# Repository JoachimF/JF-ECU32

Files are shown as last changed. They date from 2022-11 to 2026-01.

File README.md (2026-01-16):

# JF-ECU32
RC Jet Engine ECU
Details ici : https://www.usinages.com/threads/creation-dun-ecu-opensource-pour-micro-reacteur.160245/

## Démarrage du projet d'ECU opensource pour réacteurs

### Fonctionnalitées :

- Démarrage GAZ/KERO
- Fonctionnement du réacteur
- Surveillance des paramètres
- Redémarrage en vol

### Composants :
- Processeur ESP32
- Interface sonde K MAX31855

### Entrées :
- Entrée 2S - 3S pour accus LIPO ou LIION
- Entrée PPM - Gaz ou SBUS
- Entrée PPM - AUX
- Entrée compte tours IR ou HALL
- Entrée sonde K (module MAX6675 ou MAX31865)
- Entrée pression (à voir le capteur selon les plages de pression 2 bars max?)

### Sorties :
- Sortie PPM pour le moteur de démarrage
- Sortie PWM/PPM pour la pompe 10A ou ESC brushless
- Sortie PWM/PPM pour ESC de pompe numéro 2 (fumigène ou redondance, comme sur les grandeurs)
- Sorties pour 2 électrovannes (KERO/GAZ - KERO/KERO) 1A
- Sortie pour une bougies Glow ou Kero 10A
- Sortie FPORT FRSky (télémétrie)
- Sortie LED W2812

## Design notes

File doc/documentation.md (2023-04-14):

#Documentation

Detail du fonctionnement :

Les taches :

- Main
- Serveur HTTP
- Log
- ECU
- Inputs
- Htop (pour le debug)

Détail des taches :

- Main
Lance les autres taches

- Serveur HTTP
Gère l'interface WEB, s'arrete au bout de 60 secondes si pas de connection
Coupe le Wifi aussi

- Log
Enregistre dans un fichier téléchargeable par le Web tous les parmètres a partir de démarrage du moteur jusqu'a l'extinction

- ECU
Tache prioritaire qui gère le moteur en pilotant les sorties en fonction des entrée

- Inputs
Tache prioritaire qui lit les entrées

- Htop
Gestionnaire de tache qui donne le pourcentage d'utilisation du processeur par tache

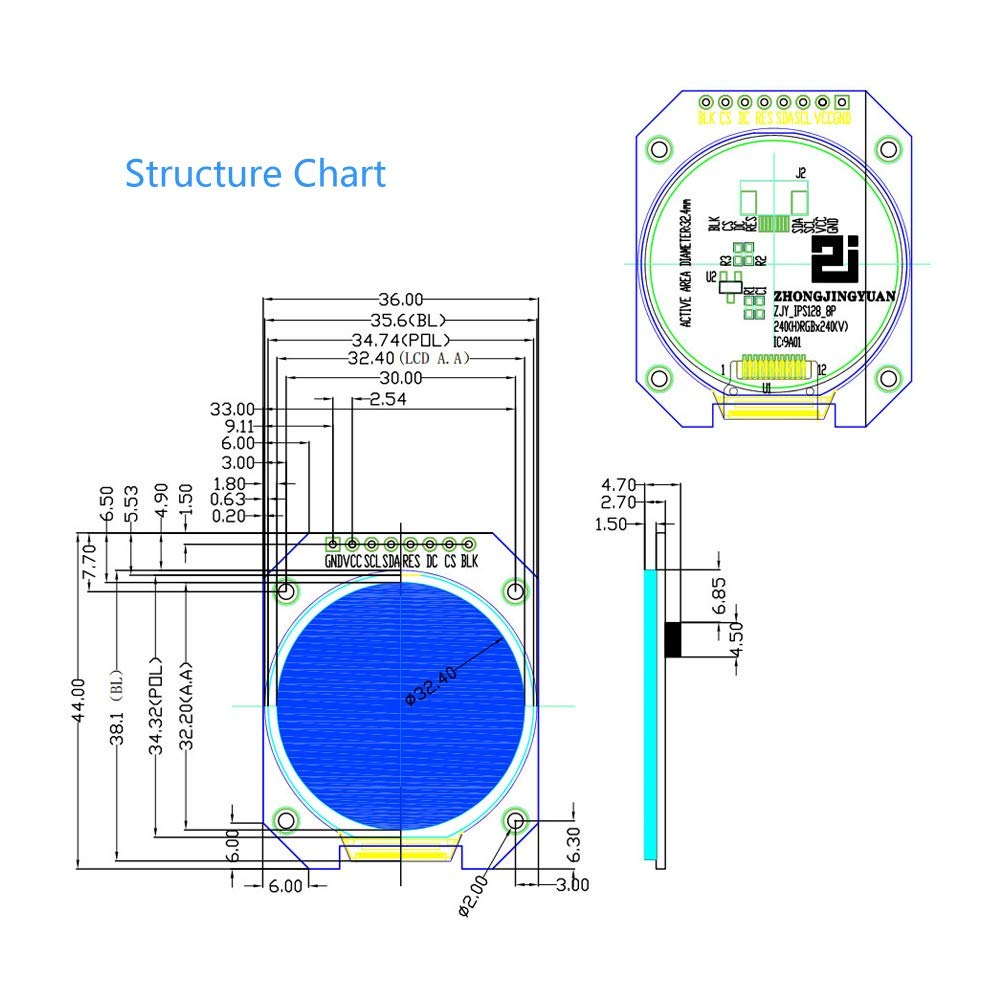
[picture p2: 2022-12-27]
Hardware/61U9lrLj2jL._SL1000_.jpg

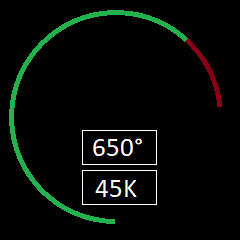
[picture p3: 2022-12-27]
doc/lcd.png

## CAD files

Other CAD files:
lcd.SLDPRT

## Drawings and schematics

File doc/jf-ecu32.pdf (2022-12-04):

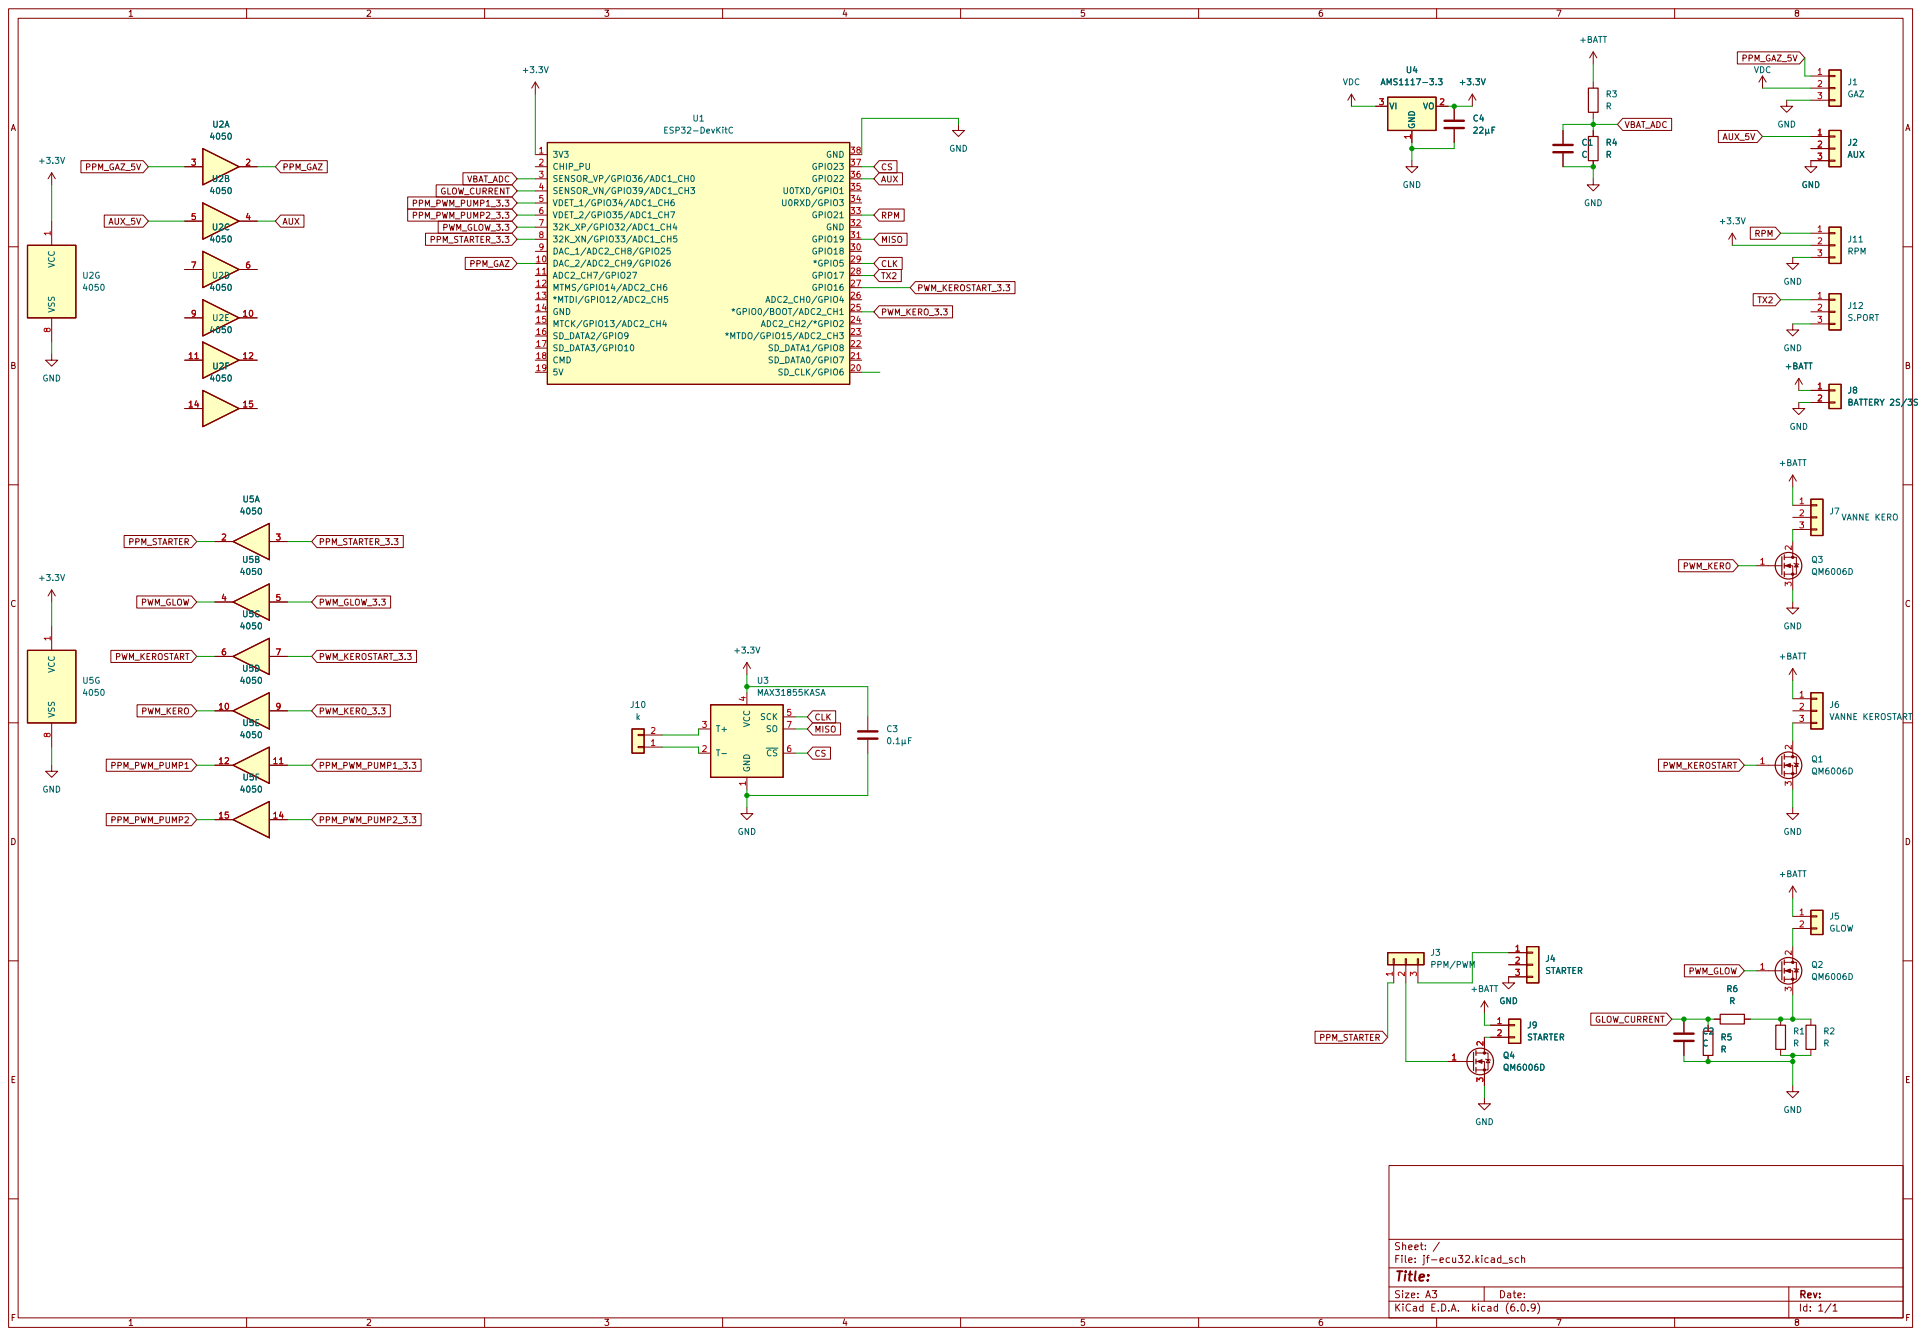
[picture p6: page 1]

+BATT GND GND GND

4 SCK 5 ~{CS} 6 SO 7 U3MAX31855KASA GND

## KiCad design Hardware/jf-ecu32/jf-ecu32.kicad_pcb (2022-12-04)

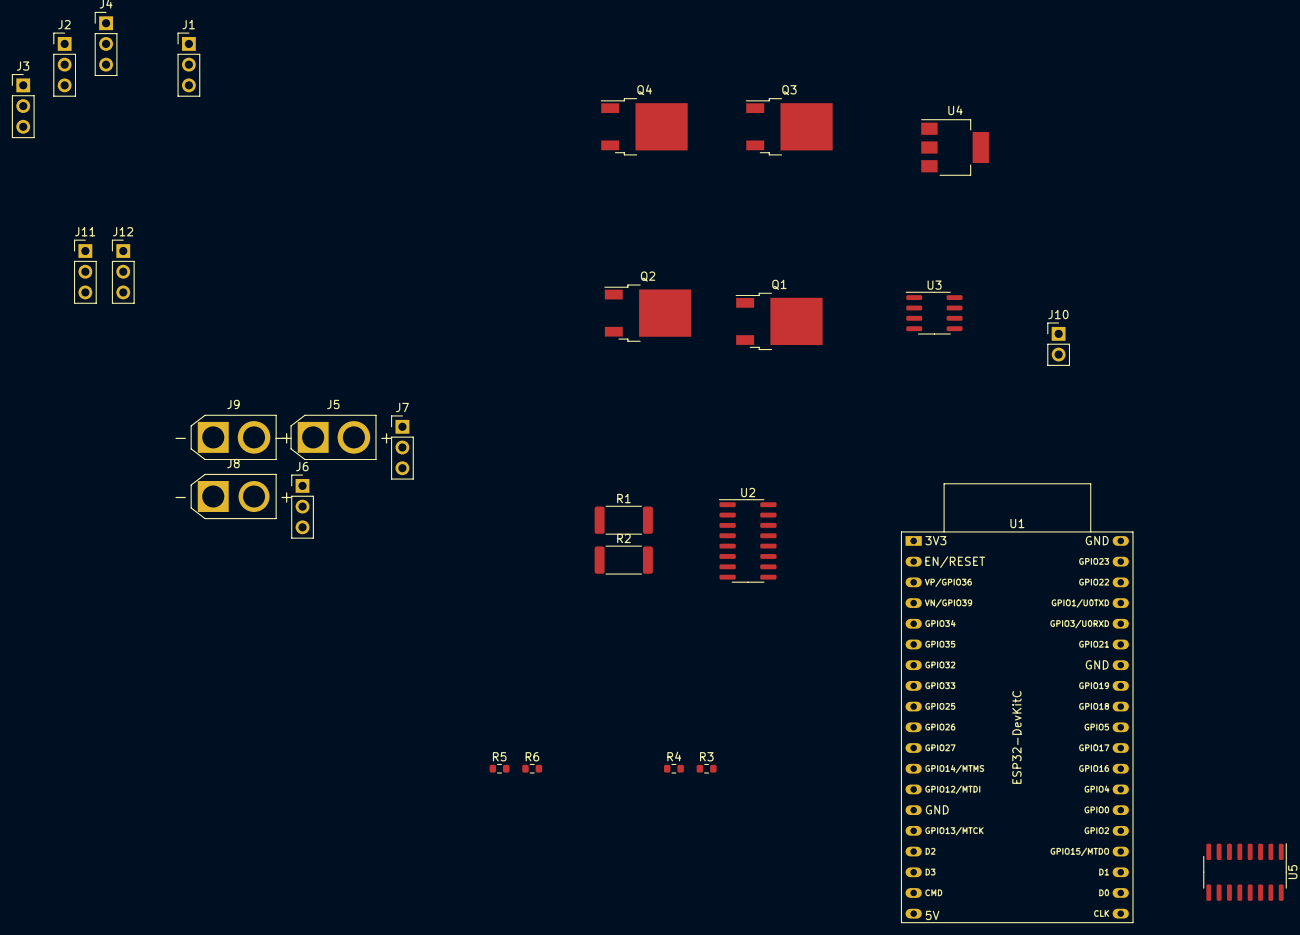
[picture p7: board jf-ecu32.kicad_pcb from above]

Board: 2 copper layers, 27 parts (0 on the bottom side), 34 nets, no tracks yet.

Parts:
J1: GAZ; PinHeader_1x03_P2.54mm_Vertical
J2: AUX; PinHeader_1x03_P2.54mm_Vertical
J3: PPM/PWM; PinHeader_1x03_P2.54mm_Vertical
J4: STARTER; PinHeader_1x03_P2.54mm_Vertical
J5: GLOW; AMASS_XT30U-F_1x02_P5.0mm_Vertical
J6: VANNE KEROSTART; PinHeader_1x03_P2.54mm_Vertical
J7: VANNE KERO; PinHeader_1x03_P2.54mm_Vertical
J8: BATTERY 2S/3S; AMASS_XT30U-M_1x02_P5.0mm_Vertical
J9: STARTER; AMASS_XT30U-F_1x02_P5.0mm_Vertical
J10: k; PinHeader_1x02_P2.54mm_Vertical
J11: RPM; PinHeader_1x03_P2.54mm_Vertical
J12: S.PORT; PinHeader_1x03_P2.54mm_Vertical
Q1, Q2, Q3, Q4: QM6006D; TO-252-2
R1, R2: R; R_2512_6332Metric
R3, R4, R5, R6: R; R_0603_1608Metric
U1: ESP32-DevKitC
U2, U5: 4050; SOP-16_3.9x9.9mm_P1.27mm
U3: MAX31855KASA; SOIC-8_3.9x4.9mm_P1.27mm
U4: AMS1117-3.3; SOT-223-3_TabPin2

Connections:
+3.3V: J11.2, U1.1 (3V3), U2.1 (VCC), U3.4 (VCC), U4.2 (VO), U5.1 (VCC)
+BATT: J5.1, J6.1, J7.1, J8.1, J9.1, R3.1
AUX: U1.36 (GPIO22), U2.4
AUX_5V: J2.1, U2.5
CLK: U1.29 (*GPIO5), U3.5 (SCK)
CS: U1.37 (GPIO23), U3.6 (~CS)
GLOW_CURRENT: R5.1, R6.1, U1.4 (SENSOR_VN/GPIO39/ADC1_CH3)
GND: J1.3, J2.3, J4.3, J8.2, J11.3, J12.3, Q1.3 (S), Q3.3 (S), Q4.3 (S), R1.2, R2.2, R4.2, R5.2, U1.38 (GND), U2.8 (VSS), U3.1 (GND), U4.1 (GND), U5.8 (VSS)
MISO: U1.31 (GPIO19), U3.7 (SO)
unnamed: J3.2, Q4.1 (G)
unnamed: J3.3, J4.1
unnamed: J5.2, Q2.2 (D)
unnamed: J6.3, Q1.2 (D)
unnamed: J7.3, Q3.2 (D)
unnamed: J9.2, Q4.2 (D)
unnamed: J10.1, U3.2 (T-)
unnamed: J10.2, U3.3 (T+)
unnamed: Q2.3 (S), R1.1, R2.1, R6.2
PPM_GAZ: U1.10 (DAC_2/ADC2_CH9/GPIO26), U2.2
PPM_GAZ_5V: J1.1, U2.3
PPM_PWM_PUMP1_3.3: U1.5 (VDET_1/GPIO34/ADC1_CH6), U5.11
PPM_PWM_PUMP2_3.3: U1.6 (VDET_2/GPIO35/ADC1_CH7), U5.14
PPM_STARTER: J3.1, U5.2
PPM_STARTER_3.3: U1.8 (32K_XN/GPIO33/ADC1_CH5), U5.3
PWM_GLOW: Q2.1 (G), U5.4
PWM_GLOW_3.3: U1.7 (32K_XP/GPIO32/ADC1_CH4), U5.5
PWM_KERO: Q3.1 (G), U5.10
PWM_KEROSTART: Q1.1 (G), U5.6
PWM_KEROSTART_3.3: U1.27 (GPIO16), U5.7
PWM_KERO_3.3: U1.25 (*GPIO0/BOOT/ADC2_CH1), U5.9
RPM: J11.1, U1.33 (GPIO21)
TX2: J12.1, U1.28 (GPIO17)
VBAT_ADC: R3.2, R4.1, U1.3 (SENSOR_VP/GPIO36/ADC1_CH0)
VDC: J1.2, U4.3 (VI)

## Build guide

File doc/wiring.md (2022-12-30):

# Attribution des pins à vérifier avec la compatibilité

## Port USB
  - RX0 GPIO3
  - TX0 GPIO1

## Sonde K - MAX31855
  - MISO  GPIO23
  - SCK   GPIO18
  - CS    GPIO5

## ADC batterie ECU
  Entrée analogique - module ADC0
  - GPIO36

## ADC Courant ECU
  Entrée analogique - module ADC0
  - GPIO39

## Voie Gaz
  Entrée PPM - module PCNT
  Entrée SBUS - module RX1
  - GPIO26 /!\Remap

## Voie AUX
  Entrée PPM - module PCNT
  - GPIO22

## Compte tours
  Entrée pulse - module PCNT
  - GPIO21

## Pompes
  Sortie PWM/PPM - module LEDC
  - 1 - GPIO
  - 2 - GPIO

## Bougie GAS/KERO
  Sortie PWM - module LEDC
  - GPIO32

## Moteur de démarrage
  Sortie PPM - module LEDC
  - GPIO33

## Electrovannes
  Sortie PWM - module LEDC
  - 1 GPIO16
  - 2 GPIO0

## Témétrie FRSKY / Futaba
  Sortie série - module TX2
  - GPIO17

## LED W2812
  - GPIO0

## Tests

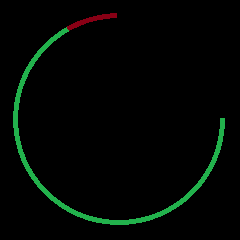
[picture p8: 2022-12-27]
doc/test.bmp

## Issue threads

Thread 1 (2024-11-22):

Max rpm

calimero4, 2024-11-22:
Hello Joachim,
Do you know how much revolutions per minute would be possible with you program?
I'm building and build so far 3 different turbines half the sice of a Lambert Kolibri and a turboprop attachment for those (140g and 1.2-1.3kg trust at 250.000 at "only" 520c, turboprop and turbine 380g) and would love to try 260.000/280.000rpm.

I've read the thread in the usinages forum and all I could find and if you still need translation to English or German I could do this!

Best regards
Matthias

JoachimF, 2024-11-22:
Hello,

With the ESP32, max RPM should be over 500.000rpm

I will test with a fonction generator, I have only a Wren55.
Thanks for your help for the German language, you see that the last code is in the dev branch.
On january 2025, I will have more much time to work on the Ecu and finish a fully automatic version.
Have you tried to compile the code ?
I need to order the last pcb, because previous have bugs or missing functions.

Regards,

Joachim

calimero4, 2024-11-22:
Hey,
Oh that sounds great!
I tried, but I'm only familiar with the arduino ide so it did not work and I'm still trying to figure out how to do this. Or is there maybe a good guideline somewhere for compiling and flashing I did not find jet?

I got all the hardware at home and would try this weekend to build onto a breadboard for testing.

Regards
Matthias

calimero4, 2024-11-22:
Here are the files for german end english!

[languages de and en.zip](https://github.com/user-attachments/files/17866832/languages.de.and.en.zip)

calimero4, 2024-11-22:
>
Have you tried to compile the code ?
>

Hello,
got it now and tried it with that result :
  fatal error: websocket_server.h: No such file or directory
   33 | #include "websocket_server.h"
      |          ^~~~~~~~~~~~~~~~~~~~
compilation terminated.

Closed 2024-11-24.

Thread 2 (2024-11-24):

Compilation Error

calimero4, 2024-11-24:
Hello Joschim,
I've tried several esp idf's versions like the current one, 5.0.7 and 4.3.4 but I get always this result (with 4.3.4 some more):

fatal error: websocket_server.h: No such file or directory
33 | #include "websocket_server.h"
| ^~~~~~~~~~~~~~~~~~~~
compilation terminated.

I changed the directory to the src folder, did a clean, opened the menuconfig and changed to 16mb and then did the build command with that result. Just building the bootboader works. Building only the app has the same result with the websocket_server.h file error.

Regards
Matthias

JoachimF, 2024-11-24:
I'll go my computer and tell you all my setup.

calimero4, 2024-11-24:
Sounds great!

calimero4, 2024-11-24:
Yes I´ll try now.

calimero4, 2024-11-24:
It worked now!
There were some warnings, i copied them into the attached .txt file.
[errors.txt](https://github.com/user-attachments/files/17893711/errors.txt)

calimero4, 2024-11-24:
The Network also appears sometimes for a short time on an Iphone and Win10 Pc but a connection is not possible. I also removed the password or tried static ip but that does not help.

JoachimF, 2024-11-24:
For the warnings, I have the sames, when I have time I solve them, but for now, it's working.

Without the good SSID and password, the ECU is AP during 1 minute with SSID JF-ECU32.
After the AP will cut wifi and http server if you don't connect to the webpage, this is to economise battery and to not makes interferences with the remote controller.

The IP is http://192.168.4.1, I think but you have mdns, http://jf-ecu32.local. There is no HTTPS, so you have to write http:// each time.

Also you can use your wifi SSID and password in the config, somewhere you can type it, I let Zigbee in this field. You have to make a full compilation when you change that. The ECU will connect, but you have to open the webpage in the minute, else the wifi and the http server will shutdown. The mdns is also working, but the IP is given by your router.

Tell me if it's ok

calimero4, 2024-11-25:
Hey, sadly no.
I tried to change the name and password in menuconfig which seems to work as the WiFi is open when the pw is removed or the name changes and I also tried the original settings and didn't touch the menuconfig and also with and without static ip.
The WiFi appears after some time, I have to guess like 20-30 seconds.
I tried to connect with an iPhone and Win10 pc but both devices are not able to connect to it.

JoachimF, 2024-11-27:
I use many types of ESP32 with 4 to 16MB, wroom, vrover etc, all are working. Are you sure you don't use C3 or S3?
Your 5 volt has enough amps?
The serial tell many things about the ECU, you can read them?

calimero4, 2024-11-28:
Hey,
i ordered the same one like you mentioned in the forum: AZDelivery ESP32 NodeMCU Dev Kit c, laser edged ESP32-WROOM-32 on the shield. I also tried an chinese wroom-32 and "found" four more to test today. It could draw up to 10 amps but is only taking around 0.113-0.116. After powerup is flashes in an sequence of 5 short flashes with an break of 3 seconds in between those after those 5 the led is on for a second and flickers, then again 5 flashes and so on. The Wifi takes around one minute untill i can see it with an iphone or the pc and if i trie to connect it says "connection failed".
I´ll try the serial monitor this evening.

Is there anything that needs to be changed in the menuconfig before build an flash?

JoachimF, 2024-11-28:
On esp32, during wifi transmission, there is 600mah peak, sometimes, the power supply can't give it instantly, so you need a capacitor close to the esp. With the serial you'll see if it reset or something else.
Also when you'll try to connect, you'll see the connection details.

As I know the is nothing to configure in the menu config, because once you are in the ecu, you can config it with the webpage.

I'll try to download it from github on another computer to see if something is missing on the git

calimero4, 2024-11-28:
> I'll try to download it from github on another computer to see if something is missing on the git

That sounds great, thank you!

Right after reset it draws around 0.06a and goes up to a maximum of 0.116a. I'll try a capacitor also when I'm home after work.

calimero4, 2024-11-28:
Here is the serial output.

`

Rebooting...
ets Jul 29 2019 12:21:46

rst:0xc (SW_CPU_RESET),boot:0x13 (SPI_FAST_FLASH_BOOT)
configsip: 0, SPIWP:0xee
clk_drv:0x00,q_drv:0x00,d_drv:0x00,cs0_drv:0x00,hd_drv:0x00,wp_drv:0x00
mode:DIO, clock div:1
load:0x3fff0030,len:6992
load:0x40078000,len:15524
ho 0 tail 12 room 4
load:0x40080400,len:3864
0x40080400: _init at ??:?

entry 0x40080650
I (29) boot: ESP-IDF v5.0.7-dirty 2nd stage bootloader
I (29) boot: compile time 16:34:04
I (29) boot: Multicore bootloader
I (33) boot: chip revision: v3.1
I (37) boot.esp32: SPI Speed      : 80MHz
I (41) boot.esp32: SPI Mode       : DIO
I (46) boot.esp32: SPI Flash Size : 4MB
I (50) boot: Enabling RNG early entropy source...
I (56) boot: Partition Table:
I (59) boot: ## Label            Usage          Type ST Offset   Length
I (67) boot:  0 nvs              WiFi data        01 02 00009000 00004000
I (74) boot:  1 otadata          OTA data         01 00 0000d000 00002000
I (82) boot:  2 phy_init         RF data          01 01 0000f000 00001000
I (89) boot:  3 ota_0            OTA app          00 10 00010000 00177000
I (96) boot:  4 ota_1            OTA app          00 11 00190000 00177000
I (104) boot:  5 storage          Unknown data     01 82 00307000 00032000
I (112) boot: End of partition table
I (116) esp_image: segment 0: paddr=00010020 vaddr=3f400020 size=2bfbch (180156) map
I (151) esp_image: segment 1: paddr=0003bfe4 vaddr=3ffb0000 size=03c2ch ( 15404) load
I (154) esp_image: segment 2: paddr=0003fc18 vaddr=40080000 size=00400h (  1024) load
I (157) esp_image: segment 3: paddr=00040020 vaddr=400d0020 size=af3cch (717772) map
I (270) esp_image: segment 4: paddr=000ef3f4 vaddr=40080400 size=196f4h (104180) load
I (303) boot: Loaded app from partition at offset 0x10000
I (303) boot: Disabling RNG early entropy source...
I (315) cpu_start: Multicore app
I (315) cpu_start: Pro cpu up.
I (315) cpu_start: Starting app cpu, entry point is 0x40081590
0x40081590: call_start_cpu1 at C:/Espressif/frameworks/esp-idf-v5.0.7/components/esp_system/port/cpu_start.c:147

I (304) cpu_start: App cpu up.
I (333) cpu_start: Pro cpu start user code
I (333) cpu_start: cpu freq: 160000000 Hz
I (333) cpu_start: Application information:
I (338) cpu_start: Project name:     JF-ECU32
I (343) cpu_start: App version:      1
I (347) cpu_start: Compile time:     Nov 24 2024 19:29:24
I (354) cpu_start: ELF file SHA256:  6ce718dce7655222...
I (360) cpu_start: ESP-IDF:          v5.0.7-dirty
I (365) cpu_start: Min chip rev:     v0.0
I (370) cpu_start: Max chip rev:     v3.99
I (374) cpu_start: Chip rev:         v3.1
I (379) heap_init: Initializing. RAM available for dynamic allocation:
I (386) heap_init: At 3FFAE6E0 len 00001920 (6 KiB): DRAM
I (392) heap_init: At 3FFB8940 len 000276C0 (157 KiB): DRAM
I (399) heap_init: At 3FFE0440 len 00003AE0 (14 KiB): D/IRAM
I (405) heap_init: At 3FFE4350 len 0001BCB0 (111 KiB): D/IRAM
I (412) heap_init: At 40099AF4 len 0000650C (25 KiB): IRAM
I (419) spi_flash: detected chip: generic
I (422) spi_flash: flash io: dio
W (427) mcpwm(legacy): legacy driver is deprecated, please migrate to `driver/mcpwm_prelude.h`
I (436) app_start: Starting scheduler on CPU0
 (441) app_start: Starting scheduler on CPU1
32mI (441) main_task: Started on CPU0
I (451) main_task: Calling app_main()
This is esp32 chip with 2 CPU cores, WiFi/BT/BLE, silicon revision 301, Currently running partition: ota_0
I (461) MAIN: Initializing NVS
I (461) NVS: Init...
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
calimero4, 2024-11-29:
Got it!

JoachimF, 2024-11-29:
The i2c library made esp crash when peripheral is not present, I have to solve that

JoachimF, 2025-04-03:
Hello,

I made a lot of improvements, the V3 pcb has an issue with the mosfet for the glow (not enough voltage to trigger it), I have modified the PCB for the V4, I have also added LEDs for the outputs and 3.3V and 5V

I have tested the read current, the battery voltage, they are ok, the ampop for the RPM hall sensor, it's working fine .
The starter brushed brake have to be tested, but most of starter now are brushless....

I added a file server to upload html files, or download logs and curves. Now all upgrade can be over the air.

I switched to ESP32 IDF 5.0.8, the documentation of the 5.0.7 is not available on Espressif website.

I hope you can now play with it.

calimero4, 2025-04-03:
Hey, sounds great!
Thennill order some Pcb's and will test :) !

JoachimF, 2025-04-13:
Hello,

The code can now preheat the engine with gas, not kerosene yet, and not complete start, it stop after 10 seconds after feeding with kero. I need more data to drive the engine to full running.
I saw that the flash memory is too small for the log, so I added on the PCB a micro SD support and there were enough room to add BMP280 (barometer).
This peripherals need new functions...

calimero4, 2025-04-13:
Hey,
Okay!
My pcb's should arrive Monday hopefully and i should have all parts here already!

JoachimF, 2025-04-17:
Hello,

How does the soldering? I made many changes on the PCB, I have to reorder a new one with SD card and glow mosfet working. I add routine to check if I2C peripheral are wired to avoid the crash, I have to do the same with the OneWire.
You should have to take the older version of the log task to store on the spiffs. I hope you can start your engine soon ;-)

JoachimF, 2025-04-19:
Hello,

I tested RPM amp with new resistors, it works well now. I added config.h, now you can select SD or SPIFFS for the logs.
I'll use this file for activate differents options.

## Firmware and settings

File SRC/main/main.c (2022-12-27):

#include <stdio.h>
#include <stdlib.h>
#include <string.h>
#include "freertos/FreeRTOS.h"
#include "freertos/task.h"
#include "freertos/queue.h"
#include "freertos/event_groups.h"
#include "freertos/semphr.h"
#include "esp_system.h"
#include "esp_wifi.h"
#include "esp_event.h"
#include "esp_vfs.h"
#include "esp_spiffs.h"
#include "nvs_flash.h"
#include "esp_err.h"
#include "esp_log.h"
#include "mdns.h"
#include "lwip/dns.h"

#include "http_server.h"

#define TAG	"MAIN"

/* FreeRTOS event group to signal when we are connected*/
static EventGroupHandle_t s_wifi_event_group;

/* The event group allows multiple bits for each event, but we only care about two events:
 * - we are connected to the AP with an IP
 * - we failed to connect after the maximum amount of retries */
#define WIFI_CONNECTED_BIT BIT0
#define WIFI_FAIL_BIT BIT1

static int s_retry_num = 0;

QueueHandle_t xQueueHttp;


static void event_handler(void* arg, esp_event_base_t event_base,
								int32_t event_id, void* event_data)
{
	if (event_base == WIFI_EVENT && event_id == WIFI_EVENT_STA_START) {
		esp_wifi_connect();
	} else if (event_base == WIFI_EVENT && event_id == WIFI_EVENT_STA_DISCONNECTED) {
		if (s_retry_num < CONFIG_ESP_MAXIMUM_RETRY) {
			esp_wifi_connect();
			s_retry_num++;
			ESP_LOGI(TAG, "retry to connect to the AP");
		} else {
			xEventGroupSetBits(s_wifi_event_group, WIFI_FAIL_BIT);
		}
		ESP_LOGI(TAG,"connect to the AP fail");
	} else if (event_base == IP_EVENT && event_id == IP_EVENT_STA_GOT_IP) {
		ip_event_got_ip_t* event = (ip_event_got_ip_t*) event_data;
		ESP_LOGI(TAG, "got ip:" IPSTR, IP2STR(&event->ip_info.ip));
		s_retry_num = 0;
		xEventGroupSetBits(s_wifi_event_group, WIFI_CONNECTED_BIT);
	}
}

void wifi_init_sta()
{
	s_wifi_event_group = xEventGroupCreate();

	ESP_LOGI(TAG,"ESP-IDF Ver%d.%d", ESP_IDF_VERSION_MAJOR, ESP_IDF_VERSION_MINOR);
	ESP_LOGI(TAG,"ESP_IDF_VERSION %d", ESP_IDF_VERSION);

//#if ESP_IDF_VERSION_MAJOR >= 4 && ESP_IDF_VERSION_MINOR >= 1
#if ESP_IDF_VERSION > ESP_IDF_VERSION_VAL(4, 1, 0)
	ESP_LOGI(TAG,"ESP-IDF esp_netif");
	ESP_ERROR_CHECK(esp_netif_init());
	ESP_ERROR_CHECK(esp_event_loop_create_default());
	esp_netif_t *netif = esp_netif_create_default_wifi_sta();
	assert(netif);
#else
	ESP_LOGE(TAG,"esp-idf version 4.1 or higher required");
	while(1) {
		vTaskDelay(1);
	}
#endif // ESP_IDF_VERSION

#if CONFIG_STATIC_IP

	ESP_LOGI(TAG, "CONFIG_STATIC_IP_ADDRESS=[%s]",CONFIG_STATIC_IP_ADDRESS);
	ESP_LOGI(TAG, "CONFIG_STATIC_GW_ADDRESS=[%s]",CONFIG_STATIC_GW_ADDRESS);
	ESP_LOGI(TAG, "CONFIG_STATIC_NM_ADDRESS=[%s]",CONFIG_STATIC_NM_ADDRESS);

	/* Stop DHCP client */
	ESP_ERROR_CHECK(esp_netif_dhcpc_stop(netif));
	ESP_LOGI(TAG, "Stop DHCP Services");

	/* Set STATIC IP Address */
	esp_netif_ip_info_t ip_info;
	memset(&ip_info, 0 , sizeof(esp_netif_ip_info_t));
	ip_info.ip.addr = ipaddr_addr(CONFIG_STATIC_IP_ADDRESS);
	ip_info.netmask.addr = ipaddr_addr(CONFIG_STATIC_NM_ADDRESS);
	ip_info.gw.addr = ipaddr_addr(CONFIG_STATIC_GW_ADDRESS);;
	esp_netif_set_ip_info(netif, &ip_info);

	/*
	I referred from here.
	https://www.esp32.com/viewtopic.php?t=5380
	if we should not be using DHCP (for example we are using static IP addresses),
	then we need to instruct the ESP32 of the locations of the DNS servers manually.
	Google publicly makes available two name servers with the addresses of 8.8.8.8 and 8.8.4.4.
	*/

	ip_addr_t d;
	d.type = IPADDR_TYPE_V4;
	d.u_addr.ip4.addr = 0x08080808; //8.8.8.8 dns
	dns_setserver(0, &d);
	d.u_addr.ip4.addr = 0x08080404; //8.8.4.4 dns
	dns_setserver(1, &d);

#endif // CONFIG_STATIC_IP

	wifi_init_config_t cfg = WIFI_INIT_CONFIG_DEFAULT();
	ESP_ERROR_CHECK(esp_wifi_init(&cfg));

	ESP_ERROR_CHECK(esp_event_handler_register(WIFI_EVENT, ESP_EVENT_ANY_ID, &event_handler, NULL));
	ESP_ERROR_CHECK(esp_event_handler_register(IP_EVENT, IP_EVENT_STA_GOT_IP, &event_handler, NULL));

	wifi_config_t wifi_config = {
		.sta = {
			.ssid = CONFIG_ESP_WIFI_SSID,
			.password = CONFIG_ESP_WIFI_PASSWORD
		},
	};
	ESP_ERROR_CHECK(esp_wifi_set_mode(WIFI_MODE_STA) );
	ESP_ERROR_CHECK(esp_wifi_set_config(ESP_IF_WIFI_STA, &wifi_config) );
	ESP_ERROR_CHECK(esp_wifi_start() );

	ESP_LOGI(TAG, "wifi_init_sta finished.");
	ESP_LOGI(TAG, "connect to ap SSID:%s password:%s",
			 CONFIG_ESP_WIFI_SSID, CONFIG_ESP_WIFI_PASSWORD);

	// wait for IP_EVENT_STA_GOT_IP
	while(1) {
		/* Wait forever for WIFI_CONNECTED_BIT to be set within the event group.
		 Clear the bits beforeexiting. */
		EventBits_t uxBits = xEventGroupWaitBits(s_wifi_event_group,
			WIFI_CONNECTED_BIT, /* The bits within the event group to waitfor. */
			pdTRUE,			/* WIFI_CONNECTED_BIT should be cleared before returning. */
			pdFALSE,			/* Don't waitfor both bits, either bit will do. */
			portMAX_DELAY);/* Wait forever. */
		if ( ( uxBits & WIFI_CONNECTED_BIT ) == WIFI_CONNECTED_BIT ){
			ESP_LOGI(TAG, "WIFI_CONNECTED_BIT");
			break;
		}
	}
	ESP_LOGI(TAG, "Got IP Address.");
}

void initialise_mdns(void)
{
	//initialize mDNS
	ESP_ERROR_CHECK( mdns_init() );
	//set mDNS hostname (required if you want to advertise services)
	ESP_ERROR_CHECK( mdns_hostname_set(CONFIG_MDNS_HOSTNAME) );
	ESP_LOGI(TAG, "mdns hostname set to: [%s]", CONFIG_MDNS_HOSTNAME);

#if 0
	//set default mDNS instance name
	ESP_ERROR_CHECK( mdns_instance_name_set("ESP32 with mDNS") );
#endif
}

static void directorySPIFFS(char * path) {
	DIR* dir = opendir(path);
	assert(dir != NULL);
	while (true) {
		struct dirent*pe = readdir(dir);
		if (!pe) break;
		ESP_LOGI(TAG,"d_name=%s/%s d_ino=%d d_type=%x", path, pe->d_name,pe->d_ino, pe->d_type);
	}
	closedir(dir);
}

esp_err_t mountSPIFFS(char * path, char * label, int max_files) {
	esp_vfs_spiffs_conf_t conf = {
		.base_path = path,
		.partition_label = label,
		.max_files = max_files,
		.format_if_mount_failed =true
	};

	// Use settings defined above toinitialize and mount SPIFFS filesystem.
	// Note: esp_vfs_spiffs_register is anall-in-one convenience function.
	esp_err_t ret = esp_vfs_spiffs_register(&conf);

	if (ret != ESP_OK) {
		if (ret ==ESP_FAIL) {
			ESP_LOGE(TAG, "Failed to mount or format filesystem");
		} else if (ret== ESP_ERR_NOT_FOUND) {
			ESP_LOGE(TAG, "Failed to find SPIFFS partition");
		} else {
			ESP_LOGE(TAG, "Failed to initialize SPIFFS (%s)",esp_err_to_name(ret));
		}
		return ret;
	}

	size_t total = 0, used = 0;
	ret = esp_spiffs_info(conf.partition_label, &total, &used);
	if (ret != ESP_OK) {
		ESP_LOGE(TAG, "Failed to get SPIFFS partition information (%s)",esp_err_to_name(ret));
	} else {
		ESP_LOGI(TAG, "Mount %s to %s success", path, label);
		ESP_LOGI(TAG, "Partition size: total: %d, used: %d", total, used);
		directorySPIFFS(path);
	}

	return ret;
}

void http_server_task(void *pvParameters);

void app_main()
{
	// Initialize NVS
	esp_err_t ret = nvs_flash_init();
	if (ret == ESP_ERR_NVS_NO_FREE_PAGES || ret == ESP_ERR_NVS_NEW_VERSION_FOUND) {
		ESP_ERROR_CHECK(nvs_flash_erase());
		ret = nvs_flash_init();
	}
	ESP_ERROR_CHECK(ret);

	// Initialize WiFi
	wifi_init_sta();

	// Initialize mDNS
	initialise_mdns();

	// Initialize SPIFFS
	ESP_LOGI(TAG, "Initializing SPIFFS");
	if (mountSPIFFS("/html", "storage", 6) != ESP_OK)
	{
		ESP_LOGE(TAG, "SPIFFS mount failed");
		while(1) { vTaskDelay(1); }
	}

	// Create Queue
	xQueueHttp = xQueueCreate( 10, sizeof(URL_t) );
	configASSERT( xQueueHttp );

	/* Get the local IP address */
	esp_netif_ip_info_t ip_info;
	ESP_ERROR_CHECK(esp_netif_get_ip_info(esp_netif_get_handle_from_ifkey("WIFI_STA_DEF"), &ip_info));
	char cparam0[64];
	sprintf(cparam0, IPSTR, IP2STR(&ip_info.ip));
	xTaskCreate(http_server_task, "HTTP", 1024*6, (void *)cparam0, 2, NULL);

	// Wait for the task to start, because cparam0 is discarded.
	vTaskDelay(10);
}

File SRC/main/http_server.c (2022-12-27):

/* HTTP Server Example
	 This example code is in the Public Domain (or CC0 licensed, at your option.)
	 Unless required by applicable law or agreed to in writing, this
	 software is distributed on an "AS IS" BASIS, WITHOUT WARRANTIES OR
	 CONDITIONS OF ANY KIND, either express or implied.
*/

#include <stdio.h>
#include <string.h>
#include <sys/stat.h>
#include <mbedtls/base64.h>

#include "freertos/FreeRTOS.h"
#include "freertos/task.h"
#include "freertos/queue.h"
#include "esp_log.h"
#include "esp_err.h"
#include "nvs.h"
#include "esp_http_server.h"

#include "http_server.h"

static const char *TAG = "HTTP";

extern QueueHandle_t xQueueHttp;

#define STORAGE_NAMESPACE "storage"

esp_err_t save_key_value(char * key, char * value)
{
	nvs_handle_t my_handle;
	esp_err_t err;

	// Open
	err = nvs_open(STORAGE_NAMESPACE, NVS_READWRITE, &my_handle);
	if (err != ESP_OK) return err;

	// Write
	err = nvs_set_str(my_handle, key, value);
	if (err != ESP_OK) return err;

	// Commit written value.
	// After setting any values, nvs_commit() must be called to ensure changes are written
	// to flash storage. Implementations may write to storage at other times,
	// but this is not guaranteed.
	err = nvs_commit(my_handle);
	if (err != ESP_OK) return err;

	// Close
	nvs_close(my_handle);
	return ESP_OK;
}

esp_err_t load_key_value(char * key, char * value, size_t size)
{
	nvs_handle_t my_handle;
	esp_err_t err;

	// Open
	err = nvs_open(STORAGE_NAMESPACE, NVS_READWRITE, &my_handle);
	if (err != ESP_OK) return err;

	// Read
	size_t _size = size;
	err = nvs_get_str(my_handle, key, value, &_size);
	ESP_LOGI(TAG, "nvs_get_str err=%d", err);
	//if (err != ESP_OK && err != ESP_ERR_NVS_NOT_FOUND) return err;
	if (err != ESP_OK) return err;
	ESP_LOGI(TAG, "err=%d key=[%s] value=[%s] _size=%d", err, key, value, _size);

	// Close
	nvs_close(my_handle);
	//return ESP_OK;
	return err;
}

int find_value(char * key, char * parameter, char * value) 
{
	//char * addr1;
	char * addr1 = strstr(parameter, key);
	if (addr1 == NULL) return 0;
	ESP_LOGD(TAG, "addr1=%s", addr1);

	char * addr2 = addr1 + strlen(key);
	ESP_LOGD(TAG, "addr2=[%s]", addr2);

	char * addr3 = strstr(addr2, "&");
	ESP_LOGD(TAG, "addr3=%p", addr3);
	if (addr3 == NULL) {
		strcpy(value, addr2);
	} else {
		int length = addr3-addr2;
		ESP_LOGD(TAG, "addr2=%p addr3=%p length=%d", addr2, addr3, length);
		strncpy(value, addr2, length);
		value[length] = 0;
	}
	ESP_LOGI(TAG, "key=[%s] value=[%s]", key, value);
	return strlen(value);
}

static esp_err_t Text2Html(httpd_req_t *req, char * filename) {
	ESP_LOGI(TAG, "Reading %s", filename);
	FILE* fhtml = fopen(filename, "r");
	if (fhtml == NULL) {
		ESP_LOGE(TAG, "fopen fail. [%s]", filename);
		return ESP_FAIL;
	} else {
		char line[128];
		while (fgets(line, sizeof(line), fhtml) != NULL) {
			size_t linelen = strlen(line);
			//remove EOL (CR or LF)
			for (int i=linelen;i>0;i--) {
				if (line[i-1] == 0x0a) {
					line[i-1] = 0;
				} else if (line[i-1] == 0x0d) {
					line[i-1] = 0;
				} else {
					break;
				}
			}
			ESP_LOGD(TAG, "line=[%s]", line);
			esp_err_t ret = httpd_resp_sendstr_chunk(req, line);
			if (ret != ESP_OK) {
				ESP_LOGE(TAG, "httpd_resp_sendstr_chunk fail %d", ret);
			}
		}
		fclose(fhtml);
	}
	return ESP_OK;
}

// Calculate the size after conversion to base64
// http://akabanessa.blog73.fc2.com/blog-entry-83.html
int32_t calcBase64EncodedSize(int origDataSize)
{
	// Number of blocks in 6-bit units (rounded up in 6-bit units)
	int32_t numBlocks6 = ((origDataSize * 8) + 5) / 6;
	// Number of blocks in units of 4 characters (rounded up in units of 4 characters)
	int32_t numBlocks4 = (numBlocks6 + 3) / 4;
	// Number of characters without line breaks
	int32_t numNetChars = numBlocks4 * 4;
	// Size considering line breaks every 76 characters (line breaks are "\ r \ n")
	//return numNetChars + ((numNetChars / 76) * 2);
	return numNetChars;
}

esp_err_t Image2Base64(char * imageFileName, char * base64FileName)
{
	struct stat st;
	if (stat(imageFileName, &st) != 0) {
		ESP_LOGE(TAG, "[%s] not found", imageFileName);
		return ESP_FAIL;
	}
	ESP_LOGI(TAG, "%s st.st_size=%ld", imageFileName, st.st_size);

	// Allocate image memory
	unsigned char*	image_buffer = NULL;
	size_t image_buffer_len = st.st_size;
	image_buffer = malloc(image_buffer_len);
	if (image_buffer == NULL) {
		ESP_LOGE(TAG, "malloc fail. image_buffer_len %d", image_buffer_len);
		return ESP_FAIL;
	}

	// Read image file
	FILE * fp_image = fopen(imageFileName,"rb");
	if (fp_image == NULL) {
		ESP_LOGE(TAG, "[%s] fopen fail.", imageFileName);
		free(image_buffer);
		return ESP_FAIL;
	}
	for (int i=0;i<st.st_size;i++) {
		fread(&image_buffer[i], sizeof(char), 1, fp_image);
	}
	fclose(fp_image);

	// Allocate base64 memory
	int32_t base64Size = calcBase64EncodedSize(st.st_size);
	ESP_LOGI(TAG, "base64Size=%d", base64Size);

	unsigned char* base64_buffer = NULL;
	size_t base64_buffer_len = base64Size + 1;
	base64_buffer = malloc(base64_buffer_len);
	if (base64_buffer == NULL) {
		ESP_LOGE(TAG, "malloc fail. base64_buffer_len %d", base64_buffer_len);
		return ESP_FAIL;
	}

	// Convert from JPEG to BASE64
	size_t encord_len;
	esp_err_t ret = mbedtls_base64_encode(base64_buffer, base64_buffer_len, &encord_len, image_buffer, st.st_size);
	ESP_LOGI(TAG, "mbedtls_base64_encode=%d encord_len=%d", ret, encord_len);

	// Write Base64 file
	FILE * fp_base64 = fopen(base64FileName,"w");
	if (fp_base64 == NULL) {
		ESP_LOGE(TAG, "[%s] open fail", base64FileName);
		return ESP_FAIL;
	}
	fwrite(base64_buffer,base64_buffer_len,1,fp_base64);
	fclose(fp_base64);

	free(image_buffer);
	free(base64_buffer);
	return ESP_OK;
}

esp_err_t Image2Html(httpd_req_t *req, char * filename, char * type)
{
	FILE * fhtml = fopen(filename, "r");
	if (fhtml == NULL) {
		ESP_LOGE(TAG, "fopen fail. [%s]", filename);
		return ESP_FAIL;
	}else{
		char buffer[64];

		if (strcmp(type, "jpeg") == 0) {
			httpd_resp_sendstr_chunk(req, "<img src=\"data:image/jpeg;base64,");
		} else if (strcmp(type, "jpg") == 0) {
			httpd_resp_sendstr_chunk(req, "<img src=\"data:image/jpeg;base64,");
		} else if (strcmp(type, "png") == 0) {
			httpd_resp_sendstr_chunk(req, "<img src=\"data:image/png;base64,");
		} else {
			ESP_LOGW(TAG, "file type fail. [%s]", type);
			httpd_resp_sendstr_chunk(req, "<img src=\"data:image/png;base64,");
		}
		while(1) {
			size_t bufferSize = fread(buffer, 1, sizeof(buffer), fhtml);
			ESP_LOGD(TAG, "bufferSize=%d", bufferSize);
			if (bufferSize > 0) {
				httpd_resp_send_chunk(req, buffer, bufferSize);
			} else {
				break;
			}
		}
		fclose(fhtml);
		httpd_resp_sendstr_chunk(req, "\">");
	}
	return ESP_OK;
}
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

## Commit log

2022-12-04 Update hardware
    [jf-ecu32.kicad_pcb, jf-ecu32.kicad_sch]
2022-12-27 Ajout des nouveautés
    [jf-ecu32.kicad_sch, lcd.SLDPRT, lcd.xlsx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]
